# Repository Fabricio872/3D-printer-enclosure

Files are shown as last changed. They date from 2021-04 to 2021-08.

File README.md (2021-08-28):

# 3D printer enclosure




 > Printed on Prusa mini

## Description

3D printer enclosure with magnetic doors.
 > Find this model on [Thingverse](https://www.thingiverse.com/thing:4817116) or [GitHub](https://github.com/Fabricio872/3D-printer-enclosure)

## Printing

 - no supports
 - no raft
 - 0.2mm layer height
 - material PETG

## Aditional materials:

 - 35X M4x16
 - 37X M4 nut
 - 4X 500mm x 500mm x 4mm plexi glass
 - 2X 500mm x 500mm x 4mm plastic or wooden plate for bottom and back side
 - 4X 18mm X 5mm neodymium magnets

## Needed printed parts
 - 4X edge.stl
 - 2X edgeFront.stl
 - 1X edgeHinge.stl
 - 1X edgeHingeBottom.stl
 - 1X handle.stl
 - 1X hinge.stl
 - 1X hingeBottom.stl
 - 2X hingeWasher.stl
 - 2X magnetBackCover.stl
 - 2X magnetGlassBackCover.stl
 - 2X magnetGlassFrontCover.stl
 - 20X washer.stl

## Assembly instructions

 1. Hinge assembly

      1. Insert nut into bottom of a hinge (hinge.stl) part with screwdriver
      > put screw onto a nut it will help you keep nut straight as you will push it into bottom of a hinge

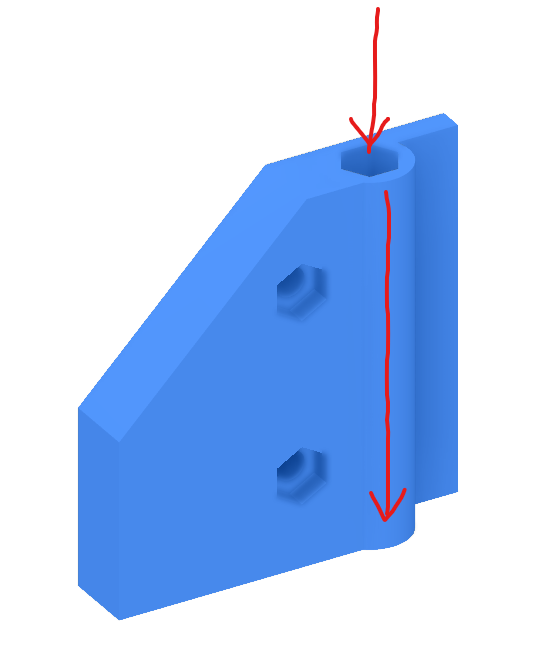
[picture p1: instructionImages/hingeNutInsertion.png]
Hinge nut insertion
      

      1. Insert nut into a hinge corner part (edgeHinge.stl, edgeHingeBottom.stl)

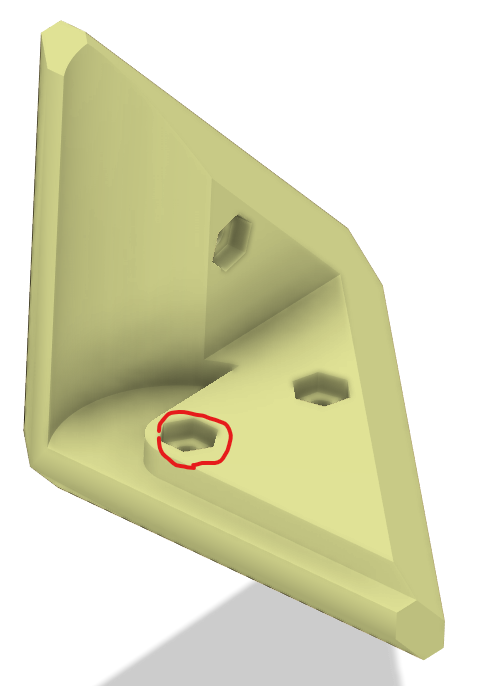
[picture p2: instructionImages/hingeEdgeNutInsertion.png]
Hinge corner nut insertion
      

      1. Place hinge part onto hinge corner as shown on picture

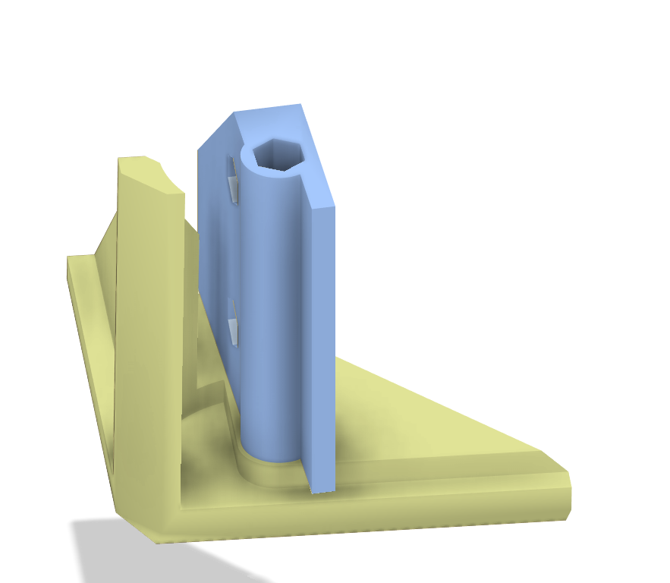
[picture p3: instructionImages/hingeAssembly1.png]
Hinge assembly 1
      

      1. Screw bolt into nut inserted in hinge edge and hinge nut and after rotating hinge to normal position it should move freely

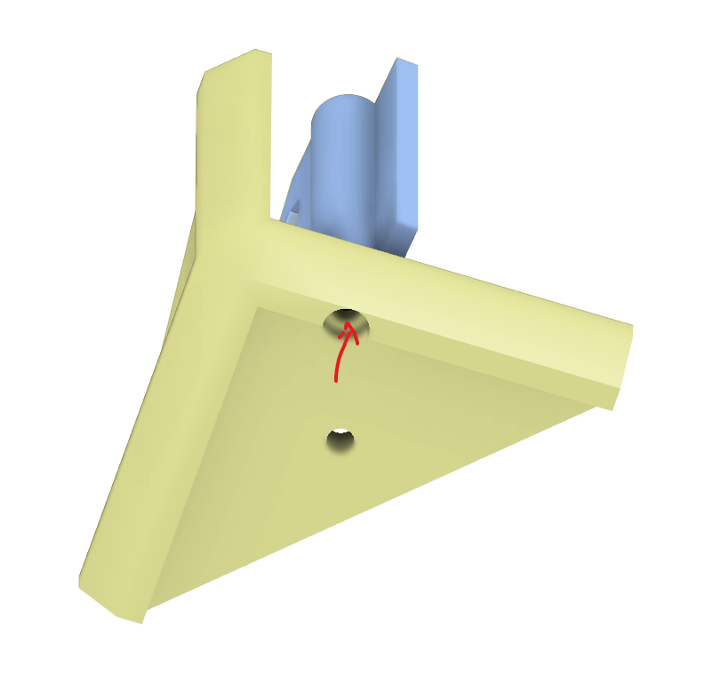
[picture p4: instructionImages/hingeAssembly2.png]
Hinge assembly 2
      

      1. Hinge should be complete now repeat this process for bottom hinge part

 1. Magnet edge part assembly

      1. Insert nuts into a magnet cover (magnetBackCover.stl)

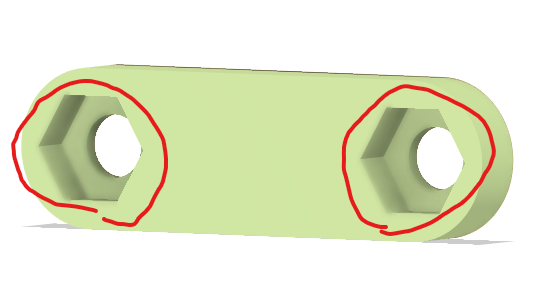
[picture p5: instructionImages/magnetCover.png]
Magnet part insertion
      

      1. Put 18mm magnet into a magnet place on magnet corner part (edgeFront.stl) and screw magnet cover on top of magnet to hold it in place

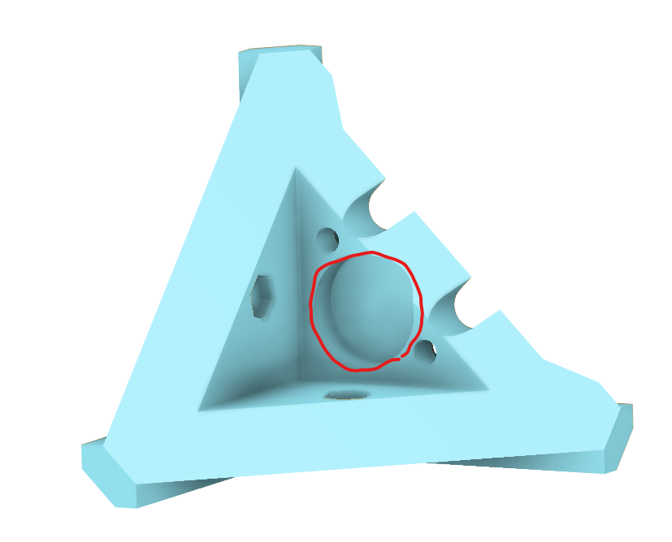
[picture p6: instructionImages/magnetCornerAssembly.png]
Magnet part assembly
      

 1. Door magnet part assembly

      1. Insert nuts on inner part of glass cover (magnetGlassBackCover.stl)

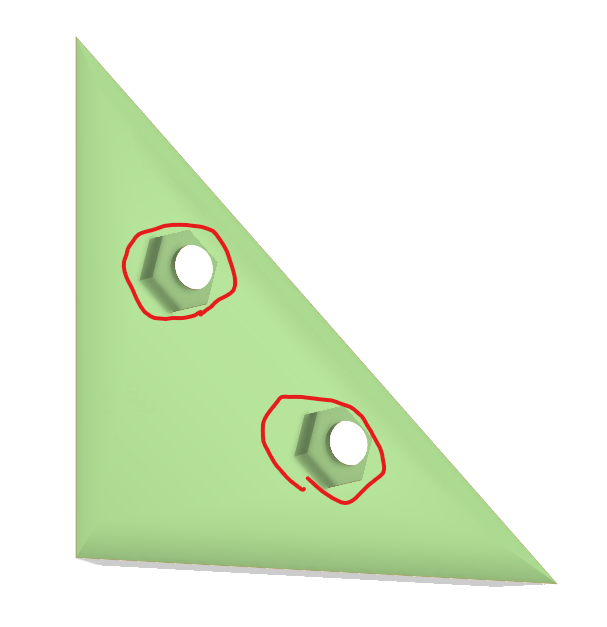
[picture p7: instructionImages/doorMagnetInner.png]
Magnet part assembly
      

      1. Drill holes into door plexi glass
      > use outer magnet part as a stencil for drilling holes for screws

      > do this on 2 corners of door glass that shares one edge of a glass

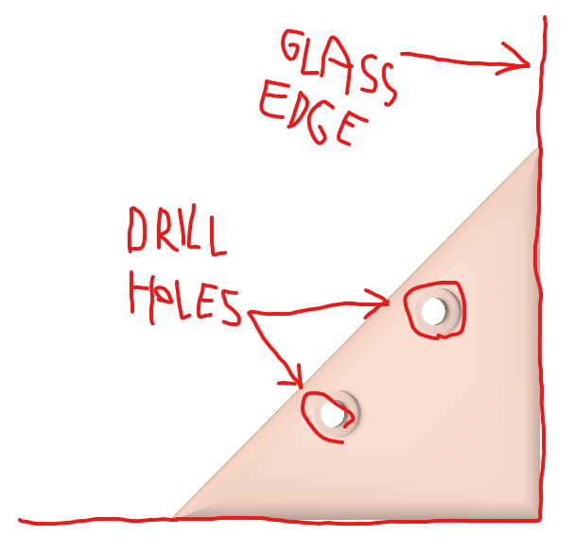
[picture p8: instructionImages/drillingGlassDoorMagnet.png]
Magnet part assembly
      

      1. Place 18mm magnet into a magnet place on outer part of glass cover (magnetGlassBackCover.stl)

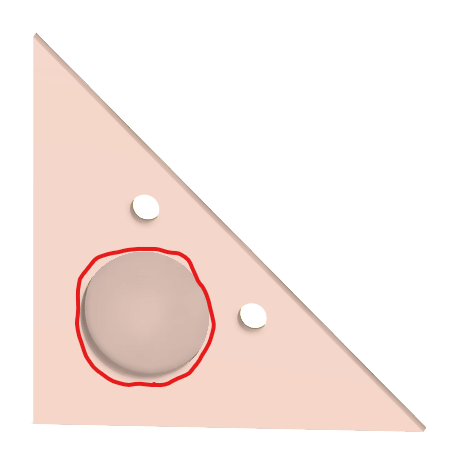
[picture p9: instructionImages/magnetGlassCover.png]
Magnet part assembly
      

      1. Put bolts through holes on outer part of glass cover and then through plexi glass and finally screw them into a inner part of glass cover (magnetGlassBackCover.stl)

      > repeat this for both pre-drilled corners

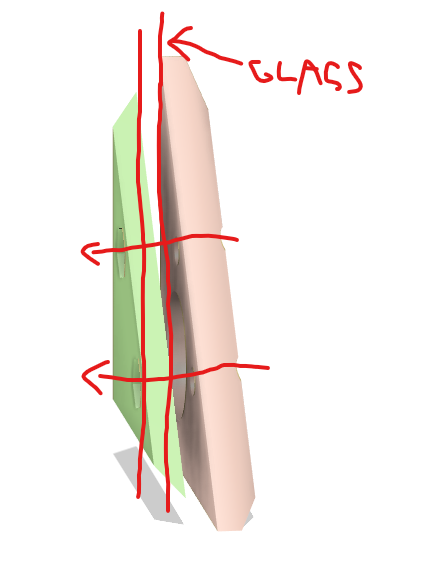
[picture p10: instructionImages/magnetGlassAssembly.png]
Magnet part assembly
      

 1. Finish assembling

      1. Insert nuts into a all remaining hexagonal holes on edge parts and hinge parts

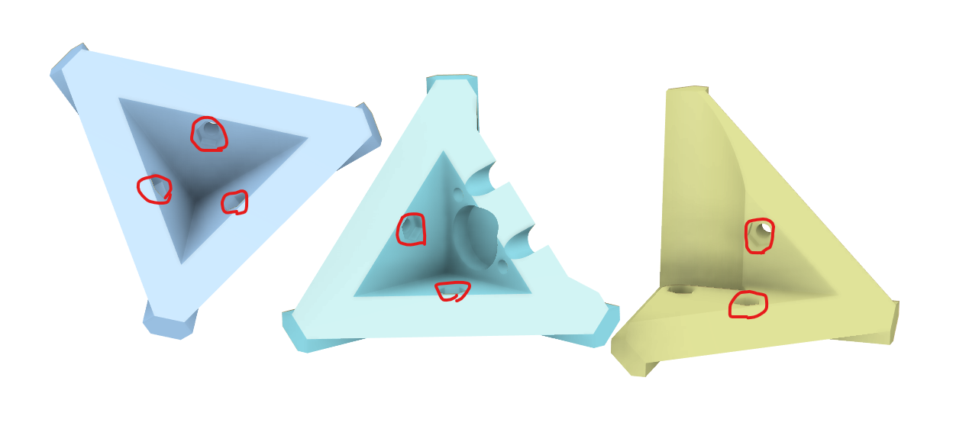
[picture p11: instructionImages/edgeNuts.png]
      

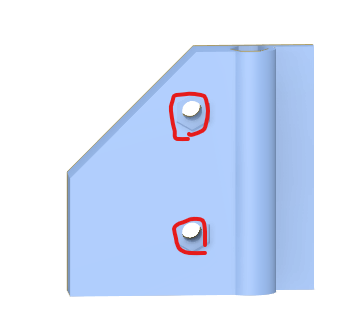
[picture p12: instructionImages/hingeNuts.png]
      

      1. Use one of the corner part as a stencil to drill holes on all corners of all plexi glass parts except one used for doors

      1. For door glass use as a stencil edge part with installed hinge

      1. Put bolt on every washer (washer.stl) and hinge washer (hingeWasher.stl)

      1. Screw bolts with washer through glass into a corner part and for door part use hinge washer with screws

      1. Put nut into a door handle (handle.stl)

      > put screw onto a nut it will help you keep nut strait as you will push it into bottom of a hinge

      1. Drill hole roughly in a middle between magnet corners on doors and use last remaining screw and washer to secure handle in place

 1. Admire your creation and consider to like this thing on Thingverse and/or GitHub

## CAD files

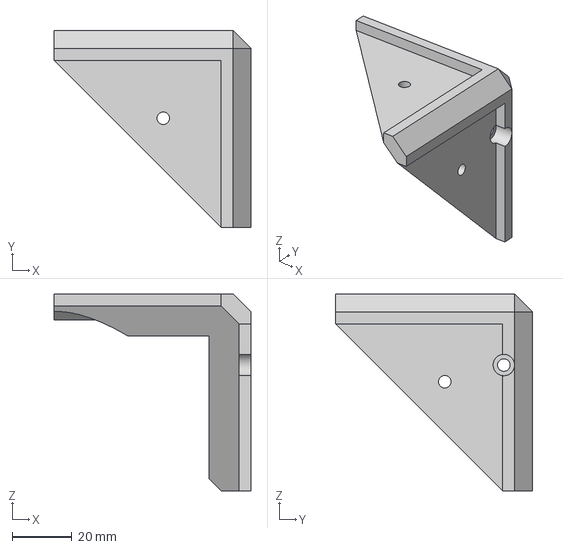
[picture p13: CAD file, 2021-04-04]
step/PrinterCaseEdges.step
66.0 x 66.0 x 66.0 mm

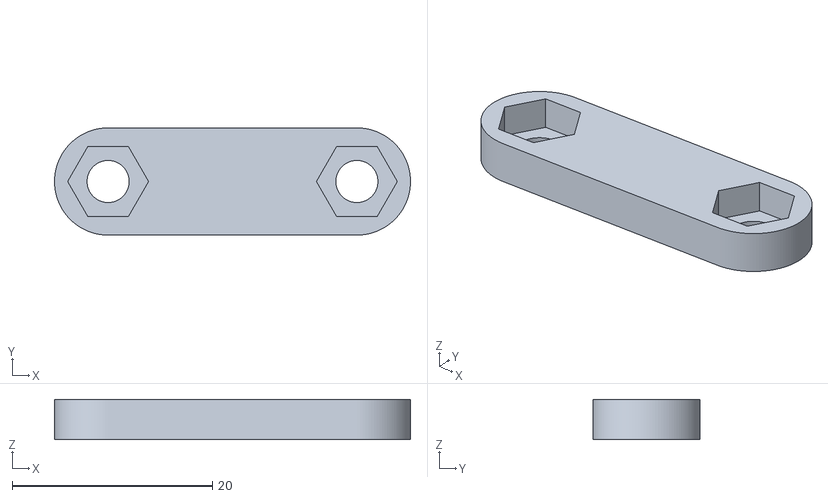
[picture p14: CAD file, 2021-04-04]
stl/magnetBackCover.stl
35.5 x 10.7 x 4.00

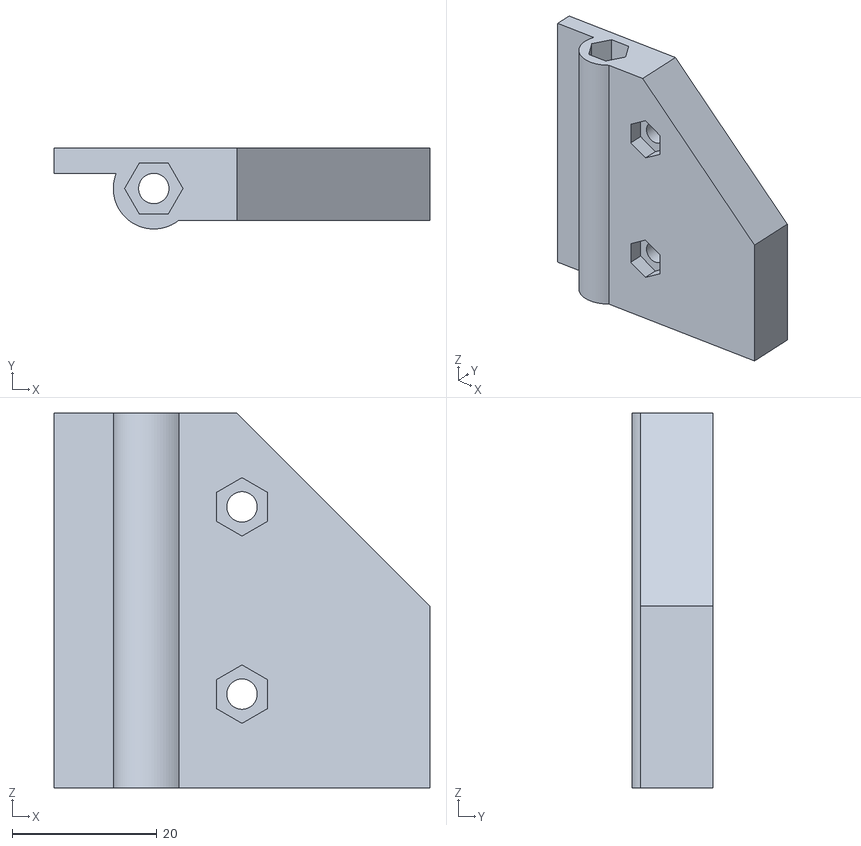
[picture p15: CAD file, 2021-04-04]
stl/hingeBottom.stl
52.0 x 11.2 x 51.8

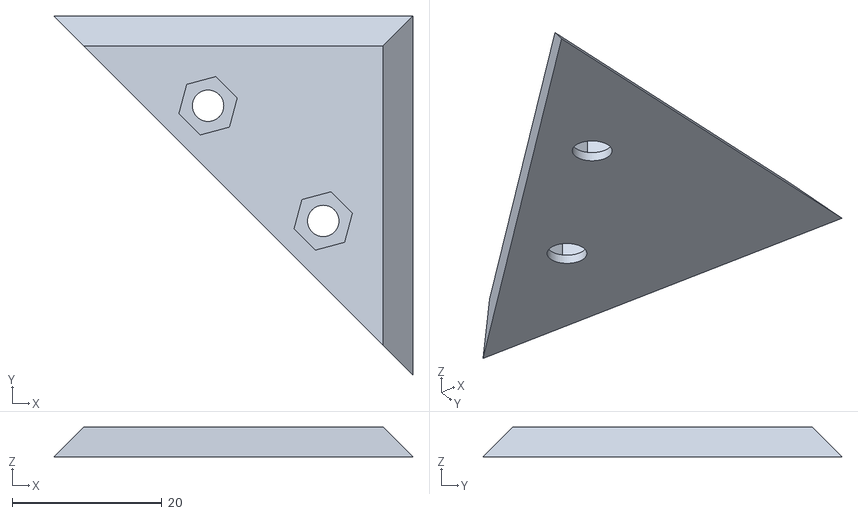
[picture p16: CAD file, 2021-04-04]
stl/magnetGlassBackCover.stl
48.0 x 48.0 x 4.00

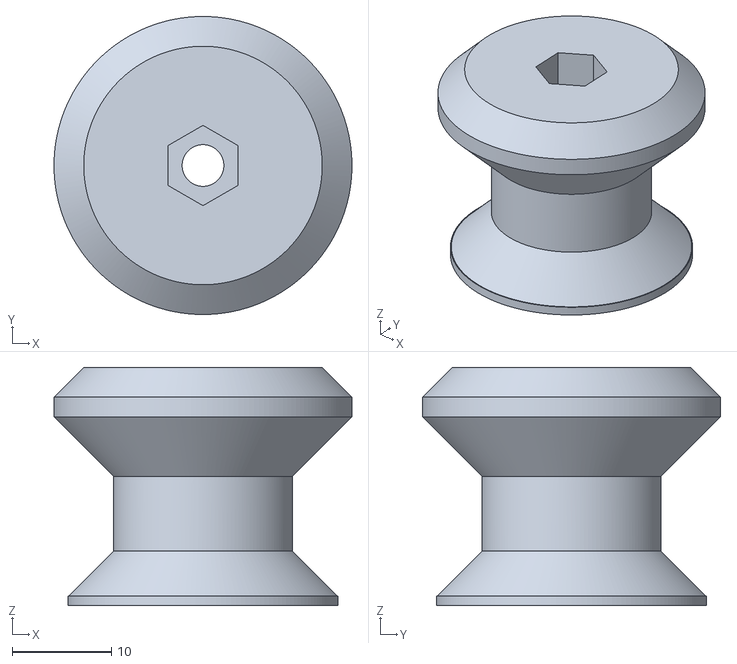
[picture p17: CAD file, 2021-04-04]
stl/handle.stl
30.0 x 30.0 x 24.0

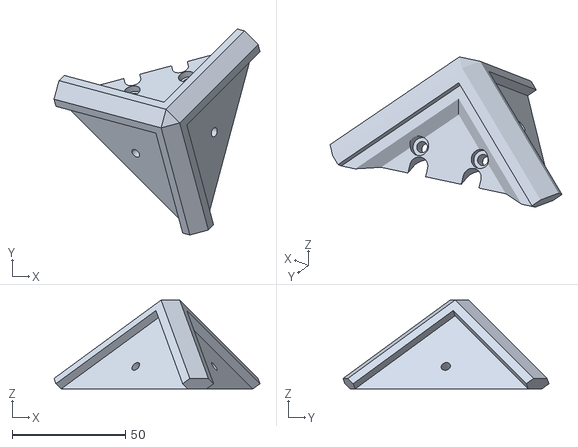
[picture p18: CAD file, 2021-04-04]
stl/edgeFront.stl
91.0 x 91.0 x 39.3

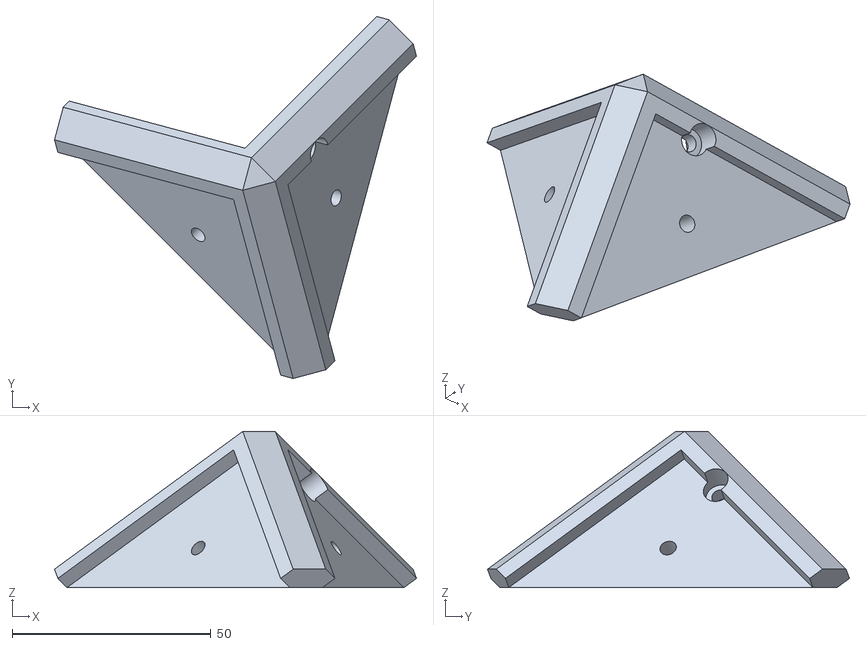
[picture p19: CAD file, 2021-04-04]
stl/edgeHinge.stl
91.0 x 91.0 x 39.3

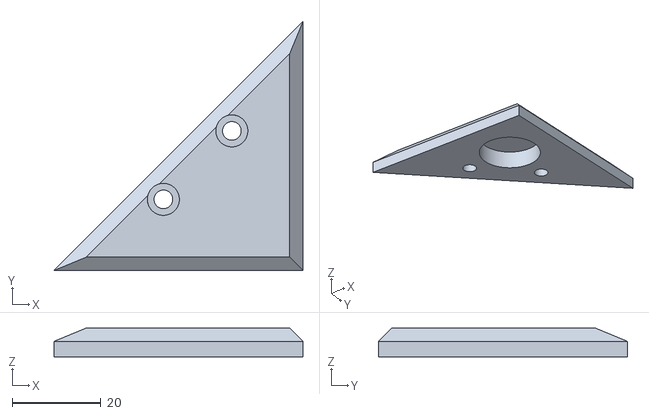
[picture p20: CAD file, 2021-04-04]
stl/magnetGlassFrontCover.stl
56.0 x 56.0 x 6.50

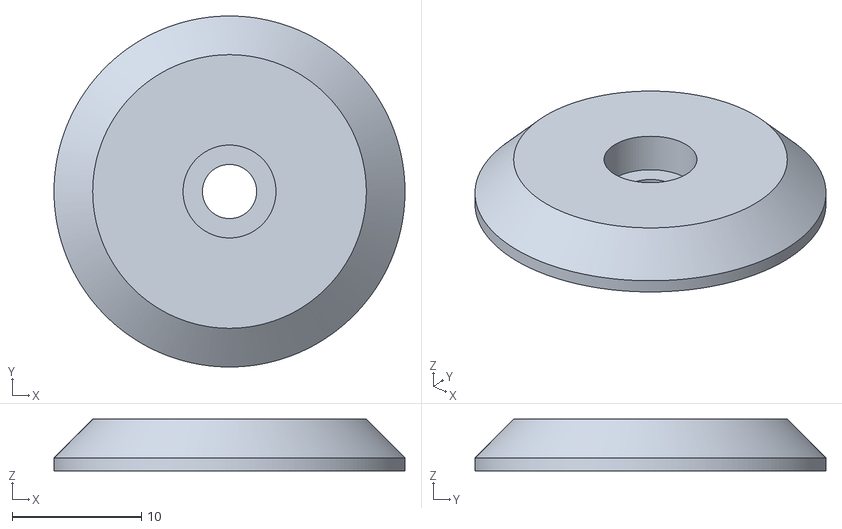
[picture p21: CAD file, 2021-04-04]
stl/washer.stl
27.2 x 27.2 x 4.00

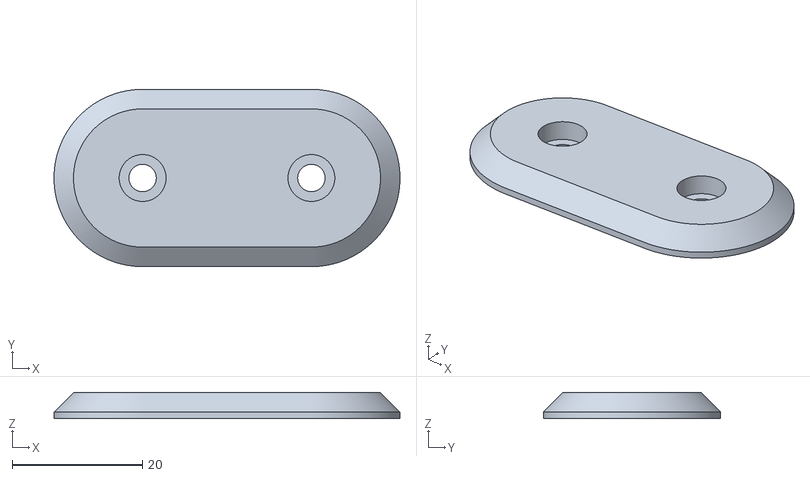
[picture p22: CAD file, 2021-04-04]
stl/hingeWasher.stl
53.1 x 27.2 x 4.00

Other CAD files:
stl/hinge.stl
stl/edgeHingeBottom.stl
stl/edge.stl

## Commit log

2021-04-04 added stl files
    [edge.stl, edgeFront.stl, edgeHinge.stl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]
2021-04-04 added step file
    [PrinterCaseEdges.step]
2021-08-28 added assembly instructions
